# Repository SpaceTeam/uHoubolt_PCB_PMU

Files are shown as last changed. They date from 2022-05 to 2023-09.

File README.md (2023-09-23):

# µHoubolt Power Management Unit (PMU) Hardware

## Features
- Altimeter capability (barometer, IMU, 2x Low Side Fet)
- 2x Low Side Fet for camera
- 1x Optocoupler for payload enable
- 2x LiIon Charger
- Flash for data logging
- 2x CAN FD

## Known Issues
- CAN Rx and Tx are swapped on CAN1 and CAN2
- No Battery Voltage Sense
- No Pyro Voltage Sense
- Same Connector for 12V and 24V
- No direct hardware arming for primary altimax
- Supply Current Sense is connected to the wrong pin
- Layout: Battery connector is hard to disconnect because it's next to the mounting hole (threaded rod)
- When powering cameras from pyro voltage, their initial current draw is large enough to trigger the overcurrent protection --> all supplied devices might get power cycled when safety pin is pulled (especially bad for ECU, might cause igniters to fire, see ECU known issues)

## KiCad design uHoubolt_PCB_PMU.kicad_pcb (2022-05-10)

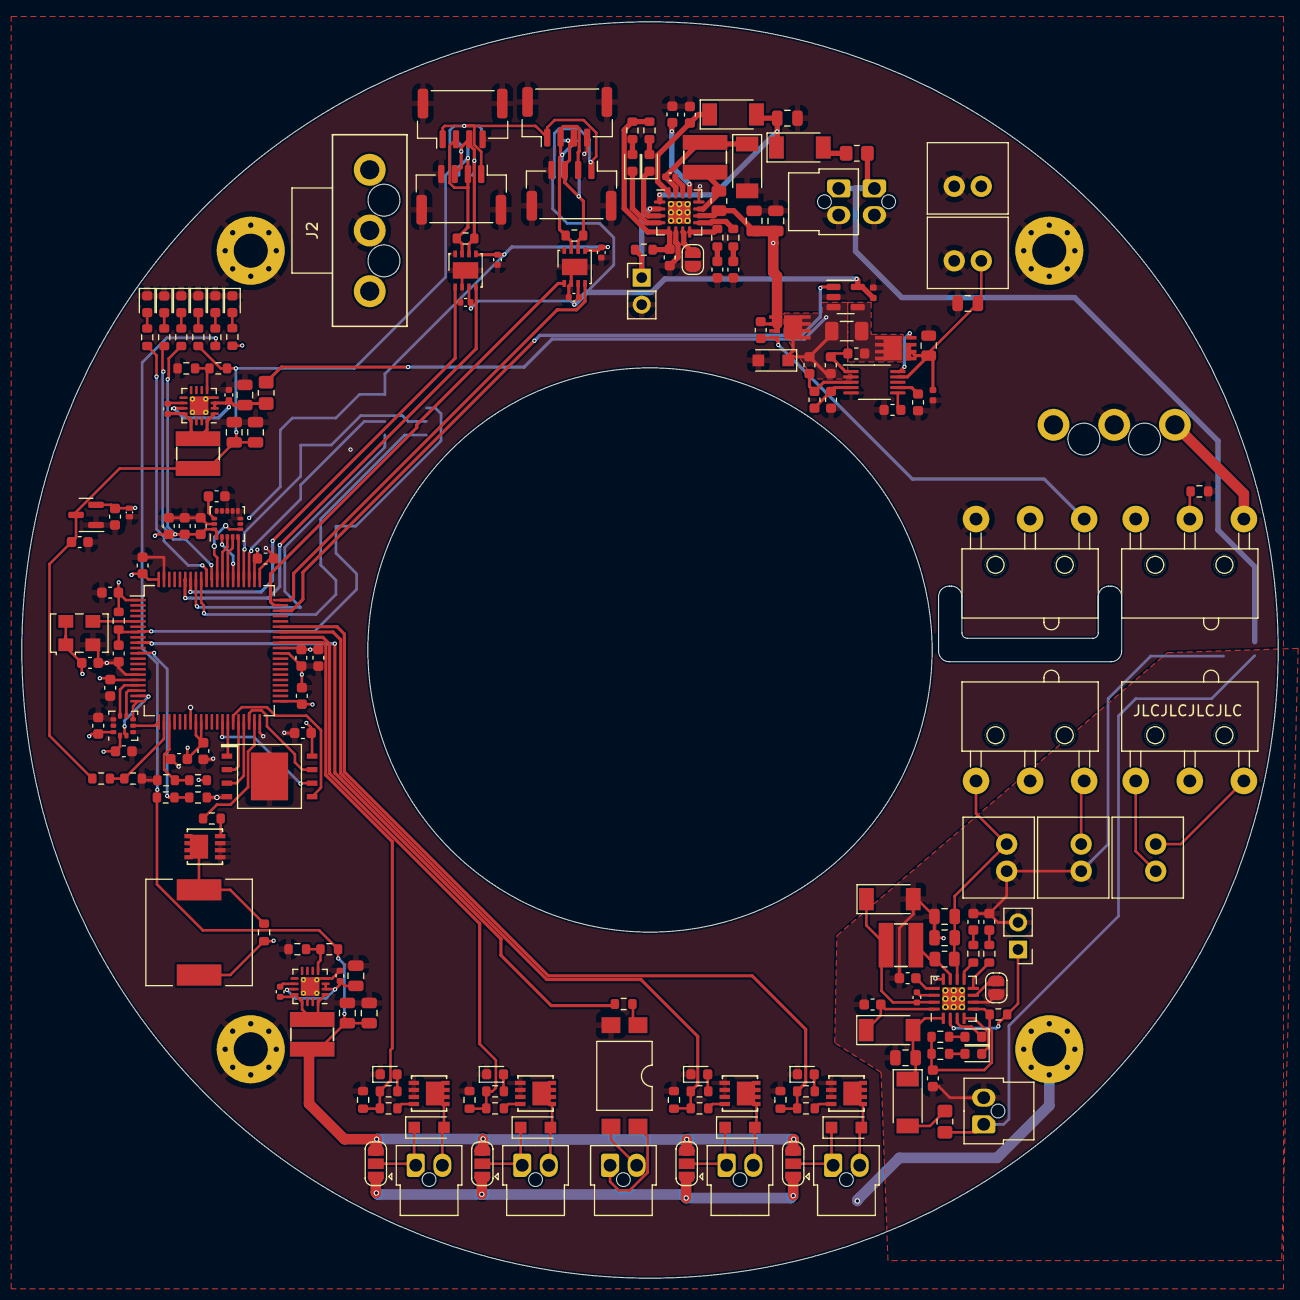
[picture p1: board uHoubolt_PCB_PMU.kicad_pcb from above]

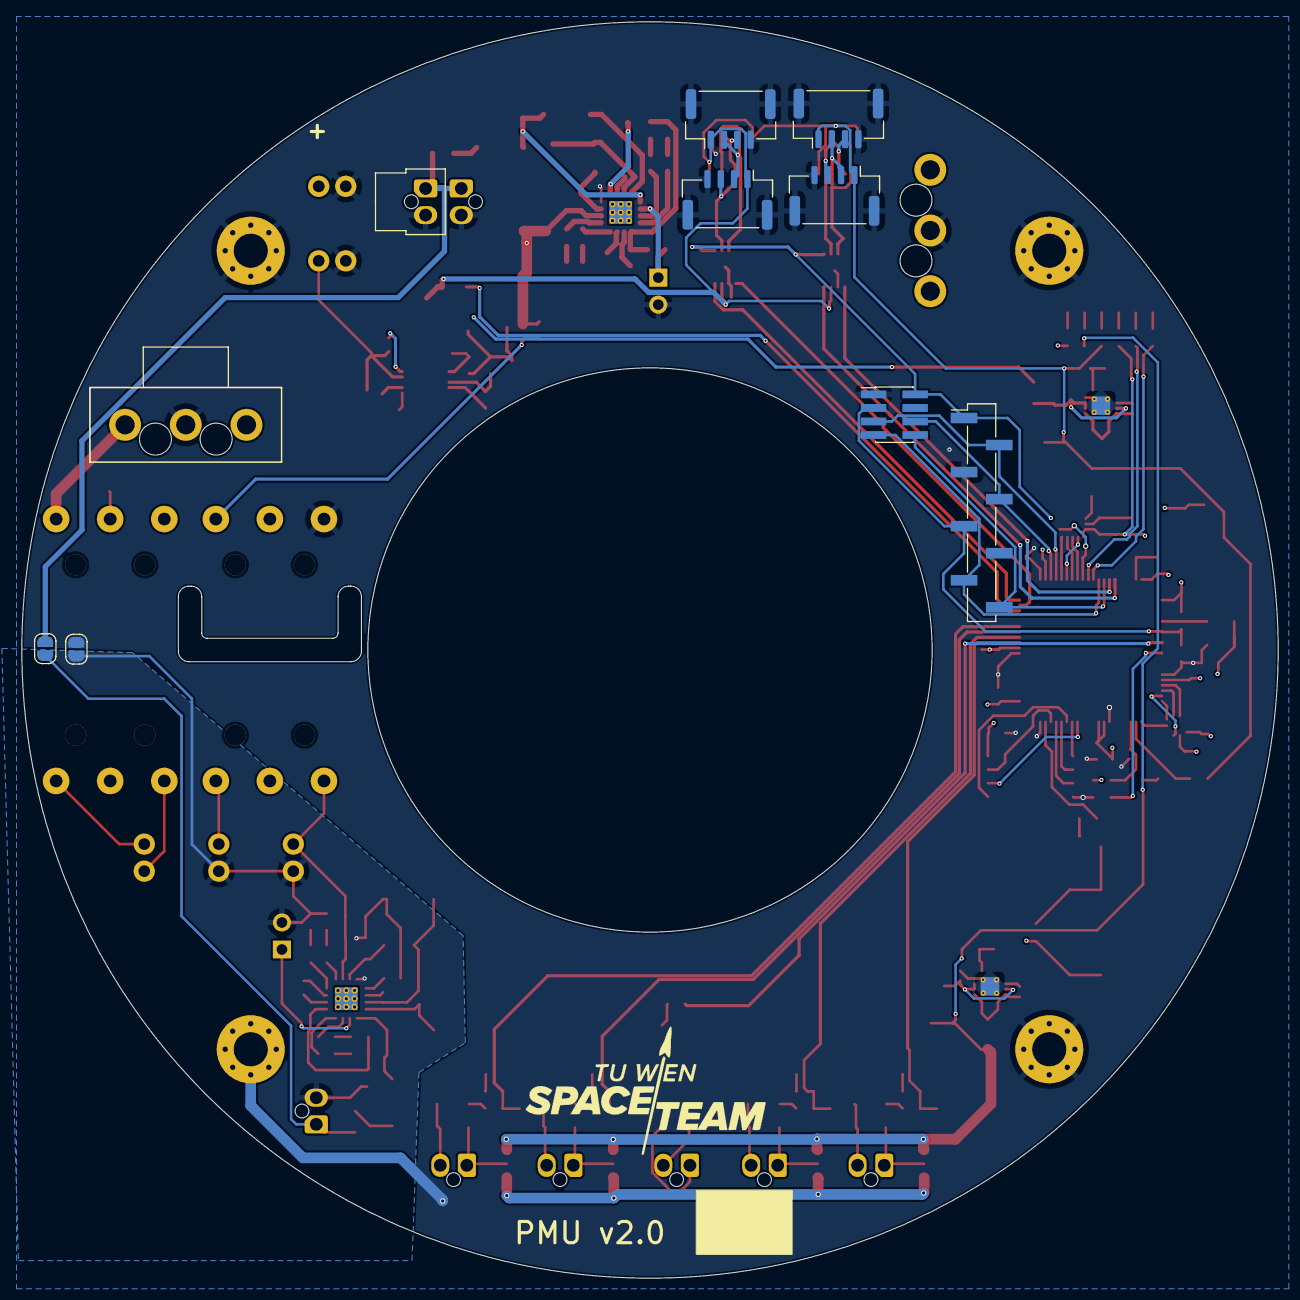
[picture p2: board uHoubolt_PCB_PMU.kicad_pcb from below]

Board: 4 copper layers, 118.0 x 118.0 mm, 212 parts (11 on the bottom side), 137 nets.

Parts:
C1: 470n; C_0603_1608Metric
C2, C10, C20, C21, C23, C25, C26, C27, C28, C29, C30, C35, C40, C41, C42, C55: 100n; C_0603_1608Metric
C3, C6, C11, C15, C19, C32, C33, C37, C38, C45, C46, C56: 100n; C_0402_1005Metric
C4, C5, C7, C14, C16, C17, C18, C43, C44, C47, C48, C52, C59, C60: 22u; C_0805_2012Metric
C8, C9, C53, C54: 4.7u; C_0603_1608Metric
C12, C13, C57, C58: 2.2n; C_0603_1608Metric
C22, C24, C31, C34, C36: 2u2; C_0603_1608Metric
C39: 10n; C_0603_1608Metric
D1: 30V; D_SOD-123F
D2: VIN; LED_0603_1608Metric
D3, D4, D19, D20: LED; LED_0603_1608Metric
D5, D6, D21, D22, D23, D24: PMEG3050EP; D_SOD-128
D7, D16: 5V; LED_0603_1608Metric
D8: TVS 3V3; SOD882D
D9: 3V3; LED_0603_1608Metric
D10, D12, D14, D17: OUT 1; LED_0603_1608Metric
D11, D13, D15, D18: Shottky; D_SOD-123F
F1, F2, F3: Fuse_Small; R_0805_2012Metric_Pad1.20x1.40mm_HandSolder
G1: SpaceTeam_LOGO; ST_Logo_new
H1, H2, H3, H4: M3; MountingHole_3.2mm_M3_Pad_Via
J1, J26: Umbilical0; Molex_Nano-Fit_105309-xx02_1x02_P2.50mm_Vertical
J2: Battery; Molex_MegaFit_1x03_Vertical
J3: Power; Molex_MegaFit_1x03_Vertical
J4: BatteryAltimax; Molex_SL_1x2_Vertical
J6: AltimaxArm; Molex_SL_1x2_Vertical
J7: Umbilical1; Molex_Nano-Fit_105309-xx02_1x02_P2.50mm_Vertical
J8, J25: RCU; Molex_SL_1x2_Vertical
J9: Debug; PinHeader_1x08_P2.54mm_Vertical_SMD_Pin1Left
J10: Debug; PinHeader_2x04_P1.27mm_Vertical_SMD
J11: AltimaxPwr; Molex_SL_1x2_Vertical
J12, J14, J16, J18: CAN1; JST_GH_BM04B-GHS-TBT_1x04-1MP_P1.25mm_Vertical
J13, J15, J17, J19: CAN2; JST_GH_BM04B-GHS-TBT_1x04-1MP_P1.25mm_Vertical
J20, J21, J22, J24: Output; Molex_Nano-Fit_105309-xx02_1x02_P2.50mm_Vertical
J23: Payload; Molex_Nano-Fit_105309-xx02_1x02_P2.50mm_Vertical
JP1, JP2, JP3, JP8: Jumper_2_Open; SolderJumper-2_P1.3mm_Open_RoundedPad1.0x1.5mm
JP4, JP5, JP6, JP7: Jumper_3_Open; SolderJumper-3_P1.3mm_Open_RoundedPad1.0x1.5mm
L1, L2, L3, L4: 4.7u; SRN4018TA-4R7M
LED1, LED2: LED_Small_Filled; LED_0603_1608Metric
LS1: Speaker; Piezo_Buzzer
Q1: BSZ0905PNSATMA1; PG_TSDSON-8
Q2: BSZ0902NSATMA1; PG_TSDSON-8
Q3, Q4, Q5, Q6, Q7: SISA88DN or similar; PowerPAK_1212-8
R1, R8, R14, R20, R21, R22, R33, R36, R39, R41, R46, R47, R48, R50: 10k; R_0603_1608Metric
R2, R3, R4, R17, R18, R31, R43, R44: R; R_0603_1608Metric
R5: NP; R_0603_1608Metric
R6: 2m; R_1206_3216Metric
R7: 0R; R_0603_1608Metric
R9: 47k; R_0603_1608Metric
R10, R16, R19, R45: 1k; R_0603_1608Metric
R11, R12, R15, R23, R24, R28, R29, R30, R32, R34, R35, R37, R38, R40, R42, R49, R51, R52: 120; R_0603_1608Metric
R13: 56k; R_0603_1608Metric
R25, R53: 750; R_0603_1608Metric
R26, R54: 2.5k; R_0603_1608Metric
R27, R55: 140m; R_0805_2012Metric
SW1: Power_1; D2F_A
SW2: Power_2; D2F_A1
SW3: Pyro_1; D2F_A
SW4: Pyro_2; D2F_A1
TH1, TH2: Thermistor_NTC; PinHeader_1x02_P2.54mm_Vertical
U1: LM5069; VSSOP-10_3x3mm_P0.5mm
U2: LMP8640 F; SOT-23-5
U3, U13: TS30041; QFN-16-1EP_3x3mm_P0.5mm_EP1.75x1.75mm_ThermalVias
U4, U14: MP26123; QFN-16-1EP_4x4mm_P0.65mm_EP2.15x2.15mm_ThermalVias
U5: STM32G491MET6-LQFP80; LQFP-80_12x12mm_P0.5mm
U6: W25Q256JV; WSON-8-8x6mm
U7: MCP1700-3302E; SOT-23
U8, U9: MCP2562FDx-x_MF; DFN-8-1EP_3x3mm_P0.65mm_EP1.55x2.4mm
U10: ICM-20602; LGA-16_3x3mm_P0.5mm_LayoutBorder3x5y
U11: LPS25HB; ST_HLGA-10_2.5x2.5mm_P0.6mm_LayoutBorder3x2y
U12: SFH617A-1X007T; SMDIP-4_W9.53mm_Clearance8mm
X1: TXC-7C; Oscillator_SMD_TXC_7C-4Pin_5.0x3.2mm

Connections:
+3V3: C2.1, C21.2, C22.2, C23.2, C24.2, C25.2, C26.2, C27.1, C28.2, C29.2, C30.2, C32.1, C33.1, C34.2, C35.2, C36.1, C39.1, C41.2, C42.1, D8.1 (K), J9.1, J10.2, R8.1, R30.1, U5.1 (VBAT), U5.16 (VDD), U5.28 (VREF+), U5.29 (VDDA), U5.41 (VDD), U5.51 (VDD), U5.62 (VDD), U5.80 (VDD), U6.8 (VCC), U7.2 (VO), U8.5 (Vio), U9.5 (Vio), U10.1 (VDDIO), U10.16 (VDD), U11.1 (VDDio), U11.10 (VDD), X1.1 (EN), X1.4 (Vdd)
+5V: C19.1, C31.1, C37.1, C38.1, C47.2, C48.2, J12.1, J13.1, J14.1, J15.1, J16.1, J17.1, J18.1, J19.1, L3.2, R43.2, R45.1, R46.1, U2.5 (V+), U7.3 (VI), U8.3 (VDD), U9.3 (VDD)
+5VP: C16.2, C17.2, JP4.3 (B), JP5.3 (B), JP6.3 (B), JP7.3 (B), L1.2, R17.2, R19.1, R20.1
+12V: C3.1, C4.1, C5.2, C6.1, C43.1, J3.1, J8.1, J25.1, LS1.1, Q2.1 (S), R10.1, R13.1, R16.1, SW3.1 (A), U1.9 (OUT), U3.2 (VCC), U3.3 (VCC), U3.11 (VCC)
+BATT: C14.1, C18.1, J2.1, Q1.1 (S), R1.1, R27.1, U4.10 (BATT)
/5V/Input: C44.2, C45.1, F1.2, U13.2 (VCC), U13.3 (VCC), U13.11 (VCC)
/5VP_Sense: R20.2, R21.1, U5.11 (PC3)
/5V_Sense: R46.2, R47.1, U5.22 (PC4)
/12V_Sense: R13.2, R14.1, U5.23 (PC5)
/BARO_INT: U5.17 (PA3), U11.7 (INT_DRDY)
/BARO_SPI1_MISO: U5.20 (PA6), U11.5 (SA0/MISO)
/BARO_SPI1_MOSI: U5.21 (PA7), U11.4 (SDA/MOSI)
/BARO_SPI1_NSS: U5.18 (PA4), U11.6 (~CS)
/BARO_SPI1_SCK: U5.19 (PA5), U11.2 (SCL/SCLK)
/BatteryCharger1/Battery: C59.1, C60.1, J4.1, R55.1, SW2.1 (A), U14.10 (BATT)
/BatteryCharger1/NTC: R50.2, TH2.1, U14.2 (NTC)
/BatteryCharger1/~ACOK: D19.1 (K), U14.3 (~ACOK)
/BatteryCharger1/~CHGOK: D20.1 (K), U14.4 (~CHGOK)
/BatteryCharger/NTC: R22.2, TH1.1, U4.2 (NTC)
/BatteryCharger/~ACOK: D3.1 (K), U4.3 (~ACOK)
/BatteryCharger/~CHGOK: D4.1 (K), U4.4 (~CHGOK)
/CAN1_H: J12.2, J14.2, J16.2, J18.2, R28.1, U8.7 (CANH)
/CAN1_L: J12.3, J14.3, J16.3, J18.3, R28.2, U8.6 (CANL)
/CAN1_RX: U5.60 (PA12), U8.4 (RXD)
/CAN1_TX: U5.59 (PA11), U8.1 (TXD)
/CAN2_H: J13.2, J15.2, J17.2, J19.2, R29.1, U9.7 (CANH)
/CAN2_L: J13.3, J15.3, J17.3, J19.3, R29.2, U9.6 (CANL)
/CAN2_RX: U5.75 (PB6), U9.4 (RXD)
/CAN2_TX: U5.74 (PB5), U9.1 (TXD)
/GND_Altimax: C52.2, C53.2, C54.2, C55.2, C57.2, C58.2, C59.2, C60.2, D22.2 (A), J4.2, J7.2, J11.2, JP3.2 (B), JP8.2 (B), TH2.2, U14.6 (~EN), U14.12 (GND)
/HSE_CLK: U5.5 (PF0-OSC_IN), X1.3 (OUT)
/IMU_INT: U5.69 (PD0), U10.6 (INT)
/IMU_NSS: U5.65 (PA15), U10.5 (~CS)
/IMU_SPI3_MISO: U5.67 (PC11), U10.4 (SAO/SD0)
/IMU_SPI3_MOSI: U5.68 (PC12), U10.3 (SDA/SDI)
/IMU_SPI3_SCK: U5.66 (PC10), U10.2 (SCL/SPC)
/LED1: R11.1, U5.71 (PD2)
/LED2: R12.1, U5.70 (PD1)
/NRST: C20.1, J9.5, J10.3, R8.2, U5.7 (PG10-NRST)
/Out0: R32.1, R33.2, R34.1, U5.52 (PC6)
/Out1: R35.1, R36.2, R37.1, U5.53 (PC7)
/Out2: R38.1, R39.2, R40.1, U5.54 (PC8)
/Out3: R42.1, R48.2, R49.1, U5.55 (PC9)
/Payload: R31.1, U5.9 (PC1)
/QSPI1_BK1_IO0: U5.35 (PE12), U6.5 (DI(IO0))
/QSPI1_BK1_IO1: U5.36 (PE13), U6.2 (DO(IO1))
/QSPI1_BK1_IO2: U5.37 (PE14), U6.3 (~WP(IO2))
/QSPI1_BK1_IO3: U5.38 (PE15), U6.7 (~RESET(IO3))
/QSPI1_BK1_NCS: U5.34 (PE11), U6.1 (~CS)
/QSPI1_CLK: U5.33 (PE10), U6.6 (CLK)
/SUPPLY_CURRENT_SENSE: U2.1, U5.58 (PA10)
/SWCLK: J9.2, J10.5, U5.64 (PA14)
/SWDIO: J9.4, J10.6, U5.63 (PA13)
/Speaker: R15.1, U5.39 (PB10)
/UART_RX: J9.8, J10.8, U5.73 (PB4)
/UART_TX: J9.7, J10.7, U5.72 (PB3)
/Vcharge: F2.1, J1.1, J26.1, JP2.1 (A)
/Vcharge1: F3.1, J7.1, JP2.2 (B)
/Vin: D1.1 (A1), F1.1, Q1.3 (D), R2.1, R5.1, R6.1, U1.2 (VIN), U2.3 (+)
GND: C1.2, C2.2, C3.2, C4.2, C5.1, C6.2, C7.2, C8.2, C9.2, C10.2, C12.2, C13.2, C14.2, C16.1, C17.1, C18.2, C19.2, C20.2, C21.1, C22.1, C23.1, C24.1, C25.1, C26.1, C27.2, C28.1, C29.1, C30.1, C31.2, C32.2, C33.2, C34.1, C35.1, C36.2, C37.2, C38.2, C39.2, C40.2, C41.1, C42.2, C43.2, C44.1, C45.2, C47.1, C48.1, D1.2 (A2), D2.1 (K), D6.2 (A), D7.1 (K), D8.2 (A), D9.1 (K), D10.1 (K), D12.1 (K), D14.1 (K), D16.1 (K), D17.1 (K), H1.1, H2.1, H3.1, H4.1, J1.2, J2.2, J3.2, J8.2, J9.3, J10.1, J12.4, J12.MP (MountPin), J13.4, J13.MP (MountPin), J14.4, J14.MP (MountPin), J15.4, J15.MP (MountPin), J16.4, J16.MP (MountPin), J17.4, J17.MP (MountPin), J18.4, J18.MP (MountPin), J19.4, J19.MP (MountPin), J25.2, J26.2, JP1.2 (B), JP3.1 (A), LED1.1 (K), LED2.1 (K), Q3.3 (S), Q4.3 (S), Q5.3 (S), Q6.3 (S), Q7.3 (S), R4.2, R9.2, R14.2, R18.2, R21.2, R33.1, R36.1, R39.1, R41.2, R44.2, R47.2, R48.1, SW1.1 (A), TH1.2, U1.5 (GND), U2.2 (GND), U3.4 (GND), U3.14 (PGND), U3.15 (PGND), U3.17 (PAD), U4.6 (~EN), U4.12 (GND), U5.15 (VSS), U5.27 (VSSA), U5.40 (VSS), U5.50 (VSS), U5.61 (VSS), U5.79 (VSS), U6.4 (GND), U6.9 (PAD), U7.1 (GND), U8.2 (VSS), U8.8 (STBY), U8.9 (PAD), U9.2 (VSS), U9.8 (STBY), U9.9 (PAD), U10.8 (FSYNC), U10.9 (GND), U10.10 (GND), U10.11 (GND), U10.12 (GND), U10.13 (GND), U10.15 (GND), U11.3 (GND), U11.8 (GND), U11.9 (GND), U12.2, U13.4 (GND), U13.14 (PGND), U13.15 (PGND), U13.17 (PAD), X1.2 (GND)
unnamed: C1.1, U1.6 (TIMER)
unnamed: C7.1, D5.2 (A), D23.1 (K), U4.1 (VCC)
unnamed: C8.1, R22.1, R23.1, R24.1, U4.5 (VREF33)
unnamed: C9.1, D5.1 (K), U4.16 (VIN)
unnamed: C10.1, U4.13 (TMR)
unnamed: C11.1, D6.1 (K), L2.1, U4.15 (SW)
unnamed: C11.2, U4.14 (BST)
unnamed: C12.1, R26.1
unnamed: C13.1, R25.1
unnamed: C15.1, L1.1, U3.1 (VSW), U3.12 (VSW), U3.13 (VSW), U3.16 (VSW)
unnamed: C15.2, U3.10 (BST)
unnamed: C40.1, U10.14 (REGOUT)
unnamed: C46.1, L3.1, U13.1 (VSW), U13.12 (VSW), U13.13 (VSW), U13.16 (VSW)
unnamed: C46.2, U13.10 (BST)
unnamed: C52.1, D21.2 (A), D24.1 (K), U14.1 (VCC)
unnamed: C53.1, R50.1, R51.1, R52.1, U14.5 (VREF33)
unnamed: C54.1, D21.1 (K), U14.16 (VIN)
unnamed: C55.1, U14.13 (TMR)
unnamed: C56.1, D22.1 (K), L4.1, U14.15 (SW)
unnamed: C56.2, U14.14 (BST)
unnamed: C57.1, R54.1
unnamed: C58.1, R53.1
unnamed: D2.2 (A), R10.2
unnamed: D3.2 (A), R23.2
unnamed: D4.2 (A), R24.2
unnamed: D7.2 (A), R19.2
unnamed: D9.2 (A), R30.2
unnamed: D10.2 (A), R32.2
unnamed: D11.1 (K), J20.1, JP4.2 (C)
unnamed: D11.2 (A), J20.2, Q4.2 (D)
unnamed: D12.2 (A), R35.2
unnamed: D13.1 (K), J21.1, JP5.2 (C)
unnamed: D13.2 (A), J21.2, Q5.2 (D)
unnamed: D14.2 (A), R38.2
unnamed: D15.1 (K), J22.1, JP6.2 (C)
unnamed: D15.2 (A), J22.2, Q6.2 (D)
unnamed: D16.2 (A), R45.2
unnamed: D17.2 (A), R42.2
unnamed: D18.1 (K), J24.1, JP7.2 (C)
unnamed: D18.2 (A), J24.2, Q7.2 (D)
unnamed: D19.2 (A), R51.2
unnamed: D20.2 (A), R52.2
unnamed: D23.2 (A), F2.2
unnamed: D24.2 (A), F3.2
unnamed: J6.1, SW4.2 (B)
unnamed: J6.2, SW4.1 (A)
unnamed: J11.1, SW2.2 (B)
unnamed: J23.1, U12.4
unnamed: J23.2, U12.3
unnamed: JP1.1 (A), U4.7 (CELLS)
unnamed: JP8.1 (A), U14.7 (CELLS)
unnamed: L2.2, R27.2, U4.11 (CSP)
unnamed: L4.2, R55.2, U14.11 (CSP)
unnamed: LED1.2 (A), R11.2
unnamed: LED2.2 (A), R12.2
unnamed: LS1.2, Q3.2 (D), R16.2
unnamed: Q1.2 (G), R1.2, SW1.2 (B)
unnamed: Q2.2 (G), U1.10 (GATE)
unnamed: Q2.3 (D), R6.2, R7.2, U2.4 (-)
unnamed: Q3.1 (G), R15.2
unnamed: Q4.1 (G), R34.2
unnamed: Q5.1 (G), R37.2
unnamed: Q6.1 (G), R40.2
unnamed: Q7.1 (G), R49.2
unnamed: R2.2, R3.1, U1.3 (UVLO)
unnamed: R3.2, R4.1, U1.4 (OVLO)
unnamed: R5.2, R7.1, U1.1 (SENSE)
unnamed: R9.1, U1.7 (PWR)
unnamed: R17.1, R18.1, U3.5 (FB)
unnamed: R25.2, U4.9 (COMPI)
unnamed: R26.2, U4.8 (COMPV)
unnamed: R31.2, U12.1
unnamed: R41.1, SW3.3 (C)
unnamed: R43.1, R44.1, U13.5 (FB)
unnamed: R53.2, U14.9 (COMPI)
unnamed: R54.2, U14.8 (COMPV)
PYRO: J3.3, JP4.1 (A), JP5.1 (A), JP6.1 (A), JP7.1 (A), SW3.2 (B)

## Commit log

2020-11-16 create kicad project with library paths
    [uHoubolt_PCB_PMU.kicad_pcb, uHoubolt_PCB_PMU.sch]
2020-12-03 add mcu
    [uHoubolt_PCB_PMU.sch]
2020-12-17 balancer connected
    [uHoubolt_PCB_PMU.sch]
2020-12-21 charge controller added
    [uHoubolt_PCB_PMU.sch]
2020-12-24 hierarchies, buck converters added
    [uHoubolt_PCB_PMU.sch]
2020-12-25 added CAN connector, current measurement and hierarchial labels
    [uHoubolt_PCB_PMU.sch]
2021-01-03 add thermistor
    [5V.sch, INA260.sch, balancer.sch]
2021-01-03 add current measurement
    [balancer.sch, uHoubolt_PCB_PMU.sch]
2021-01-03 add resistor values of regulator
    [balancer.sch, uHoubolt_PCB_PMU.sch]
2021-01-03 connect labels to muC
    [balancer.sch, uHoubolt_PCB_PMU.sch]
2021-01-03 change labels
    [uHoubolt_PCB_PMU.sch]
2021-01-03 add metadata
    [balancer.sch, uHoubolt_PCB_PMU.sch]
2021-01-03 small fix balancer schematic
    [balancer.sch]
2021-01-03 replace mosfet
    [uHoubolt_PCB_PMU.sch]
2021-01-03 change voltage divider values
    [uHoubolt_PCB_PMU.sch]
2021-01-03 add voltage divider sys_load
    [uHoubolt_PCB_PMU.sch]
2021-01-03 bat+ lable change, change mosfets balancer, remove sys_load
    [balancer.sch, uHoubolt_PCB_PMU.sch]
2021-01-04 Add descriptions
    [balancer.sch, uHoubolt_PCB_PMU.sch]
2021-01-04 change description
    [uHoubolt_PCB_PMU.sch]
2021-01-12 unify notation, connect NoConnects, revise balancer, add output connector
    [balancer.sch, uHoubolt_PCB_PMU.sch]
2021-01-12 add NoConnects, add capacitor footprints, add pulldown to Q1
    [balancer.sch, uHoubolt_PCB_PMU.sch]
2021-01-13 solve ERC errors
    [uHoubolt_PCB_PMU.sch]
2021-01-17 connect power flags, update main
    [balancer.sch, uHoubolt_PCB_PMU.sch]
2021-04-07 add mosfet in schematic, draw outer bounds of pcb
    [balancer.sch, uHoubolt_PCB_PMU.kicad_pcb, uHoubolt_PCB_PMU.sch]
2021-04-11 add ignition bus, placement 75% done
    [balancer.sch, uHoubolt_PCB_PMU.kicad_pcb, uHoubolt_PCB_PMU.sch]
2021-04-18 add footprints of 2 shunts
    [uHoubolt_PCB_PMU.sch]
2021-04-19 placing components 85% done
    [uHoubolt_PCB_PMU.kicad_pcb]
2021-05-13 new processor chip and add some suddenly missing footprints
    [uHoubolt_PCB_PMU.kicad_pcb]
2021-12-10 removed old project (moved to branch old)
    [5V.sch, balancer.sch, uHoubolt_PCB_PMU.kicad_pcb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]
2021-12-10 added new PMU project
    [uHoubolt_PCB_PMU.kicad_pcb, uHoubolt_PCB_PMU.sch, uHoubolt_PCB_PowerSwitch.step]
2021-12-21 Added ECU to PMU
    [uHoubolt_PCB_PMU.kicad_pcb, uHoubolt_PCB_PMU.sch]
2021-12-21 Revert "Added ECU to PMU"
    This reverts commit 9e77d8288f64199274fc49822545c9b66851eb22.
    [uHoubolt_PCB_PMU.kicad_pcb, uHoubolt_PCB_PMU.sch]
2021-12-21 PMU ECU Combo (Fixed git mistakes)
    [uHoubolt_PCB_PMU.sch]
2021-12-22 PMU Layout
    [uHoubolt_PCB_PMU.kicad_pcb, uHoubolt_PCB_PMU.sch]
2021-12-22 New Layout
    [D2F_A.step.SLDASM, D2F_A1.step.SLDASM, SOLID-13.step.SLDPRT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]
2021-12-22 Release Version of PMU V1
    [D2F_A.step.SLDASM, D2F_A1.step.SLDASM, SOLID-13.step.SLDPRT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]
2021-12-22 added new step file
    [uHoubolt_PCB_PowerSwitch.step]
2022-04-14 WIP PMU V2
    [uHoubolt_PCB_PMU.kicad_pcb, uHoubolt_PCB_PMU.kicad_sch]
2022-04-29 [WIP] Fixed References and Preps for PMUv2
    [BatteryCharger.kicad_sch, Output.kicad_sch, uHoubolt_PCB_PMU.kicad_sch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]
2022-04-30 [WIP] PMUv2
    [5V_SMPS.kicad_sch, BatteryCharger.kicad_sch, Output.kicad_sch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]
2022-05-10 PMU v2 WIP
    [BatteryCharger.kicad_sch, uHoubolt_PCB_PMU.kicad_pcb, uHoubolt_PCB_PMU.kicad_sch]
2022-05-11 PMU V2 "ready to order"?
    [BatteryCharger.kicad_sch, uHoubolt_PCB_PMU.kicad_sch]
2022-08-10 V3 Init Commit
    Fix of known issues of v2
    [Output.kicad_sch]
2022-08-16 Schematic: Changed Polarity of umbilical connectors Schematic: Added TVS diode to battery_sense Schematic: Some minor prettyfication
    Still wrong: Main LiIon Charger Enable connect to STM32
    [5V_SMPS.kicad_sch, Output.kicad_sch, uHoubolt_PCB_PMU.kicad_sch]
2022-08-18 PMU V3 "ready to order?"
    ready to validate changes
    [5V_SMPS.kicad_sch, Output.kicad_sch, uHoubolt_PCB_PMU.kicad_pcb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]
2022-08-18 Revert "PMU V3 "ready to order?""
    This reverts commit e5aaef69110c3557dfda333950fee24891806424.
    [5V_SMPS.kicad_sch, Output.kicad_sch, uHoubolt_PCB_PMU.kicad_pcb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]
